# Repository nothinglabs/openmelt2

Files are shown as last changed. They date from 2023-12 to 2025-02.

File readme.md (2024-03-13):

# Open Melt

Open Melt is an open-source translational drift (aka "melty brain") robot controller based on Arduino.

A translational drift robot spins its entire body using its drive wheel(s), but is still capable of directional control by modulating motor power at certain points each rotation.  To achieve this - the rate of rotation must be tracked.

<div align="center">
<table class="center"><tr><td align="center">
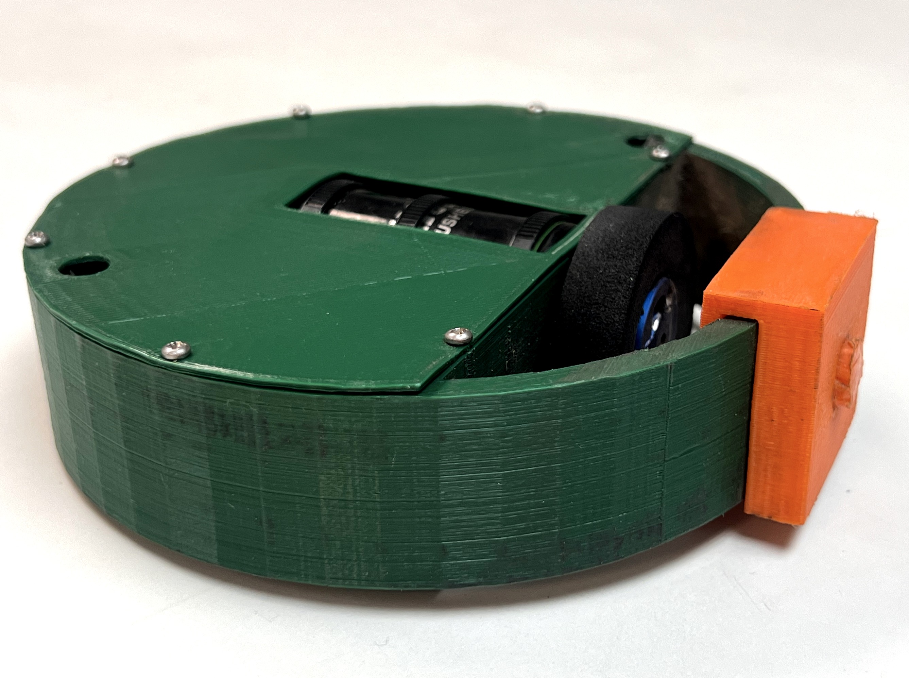
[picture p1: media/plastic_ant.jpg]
<a href="./antweight_reference_platform/"><br>Antweight Reference Platform</a</td>
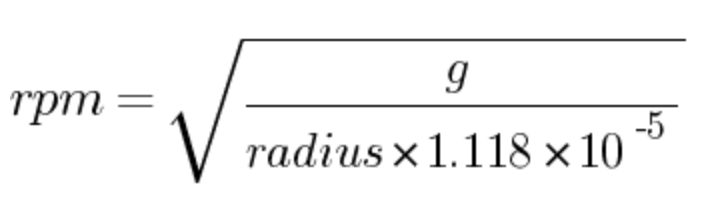
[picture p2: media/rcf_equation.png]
<td valign="center"></td>
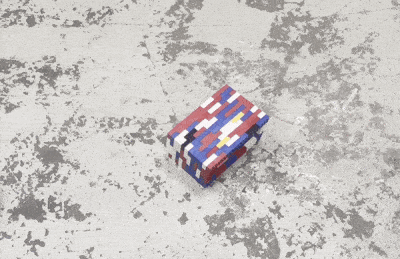
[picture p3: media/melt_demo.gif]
<td align="center"><br>~2300rpm</td>
</td></tr></table></div>

Open Melt uses an accelerometer to calculate the rate of rotation based on G-forces around a given radius (centrifugal force).  For example - an accelerometer mounted 4cm from the center of rotation experiencing 145g can be [calculated](https://druckerdiagnostics.com/g-force-calculator/) to indicate 1800rpm rotation.

An LED is turned on once per rotation - giving the appearance of the "front" of the robot.  This lets the driver see the expected direction of translation.  The user can adjust the heading beacon by moving the remote control left or right.  This allows for steering and correction of minor tracking errors.

The system can work with robots using either one or two drive motors.

It has been tested up to 3200rpm - and can likely work at significantly higher speeds.

Version 2 of the project is a complete recode (previously native Atmega/AVR).  The move to Arduino was done to make it more accessible and potentially portable to non-AVR platforms.

Open Melt was developed by Rich Olson ([nothinglabs.com](http://www.nothinglabs.com) / rich@nothinglabs.com) and is provided under the [Creative Commons Attribution-NonCommercial-ShareAlike](https://creativecommons.org/licenses/by-nc-sa/4.0/deed.en) license.

A longer demo video and some background on Open Melt are available at this [blog post](http://www.nothinglabs.com/open-melt-2/).

#### For a complete parts list, 3d print files and build notes see the [antweight reference platform](./antweight_reference_platform/).

## Demo Video

https://github.com/nothinglabs/openmelt2/assets/3834997/7247756d-c1fe-4b85-9fc3-9274c0709dcb

## General Hardware Requirements

- Arduino Micro (or other Atmega32u4 5v 16MHz Arduino / compatible)
- [H3LIS331](https://www.st.com/resource/en/datasheet/h3lis331dl.pdf) 400g accelerometer (recommended: [Adafruit H3LIS331 breakout](https://www.adafruit.com/product/4627))
- RC Transmitter / Receiver 
- Heading LED
- Motor Driver(s)
- Motor(s)

Use of an **Atmega328-based Arduino is not supported** due to lack of adequate interrupt pins.

The HSLI311 is a 3v part - but the Adafruit breakout includes a 3v<->5v level converter to make interfacing with the Arduino easy.  Alternatively, [Sparkfun's H3LIS331DL Breakout](https://www.sparkfun.com/products/14480) has been verified to work when used in conjunction with the [SparkFun 3v<->5v Logic Level Converter](https://www.sparkfun.com/products/12009).

## 1 vs. 2 Wheels
Open Melt generates signals for 2 motors independent of how many are connected.  Motor 2 is powered for the same portion of each rotation as motor 1 (trailing 180 degrees out of phase).

<div align="center">
<table class="center"><tr><td>
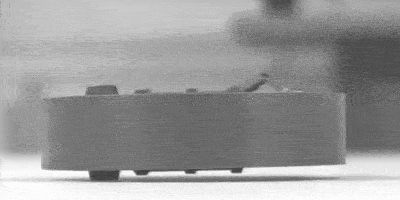
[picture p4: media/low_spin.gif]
</td>

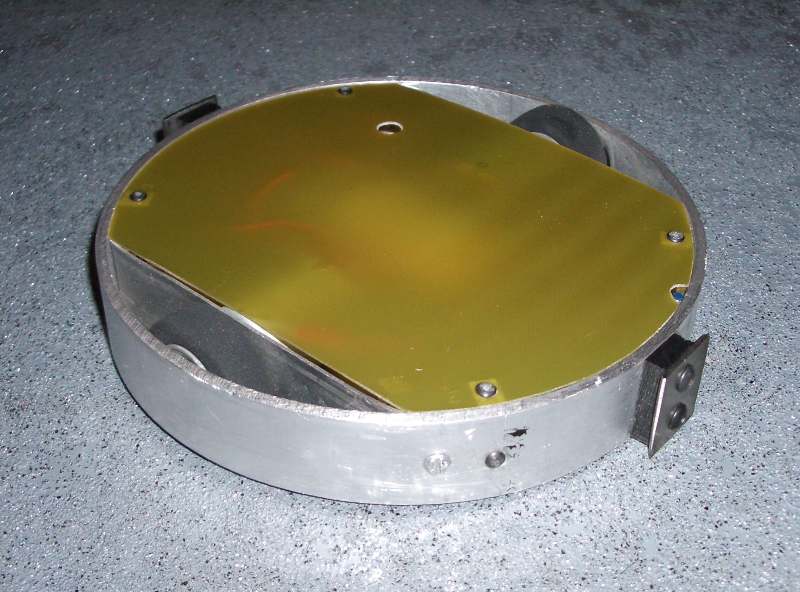
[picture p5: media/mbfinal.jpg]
<td></td>
</td></tr></table></div>

In a 1 wheel robot - the unsupported end scrapes the ground during spin-up - but then levitates when it reaches speed.  

## Accelerometer Placement
The accelerometer must be positioned so that it experiences no more than 400g at the robot's anticipated max rotation speed. A [centrifuge calculator](https://druckerdiagnostics.com/g-force-calculator/) may be used to determine this.

Open Melt provides an interactive setup routine that makes precise placement or orientation of the accelerometer unnecessary.

Alignment of the accelerometer off-axis will result in a linear error - which has the same effect as reducing the radius of rotation.  Placing will the accerometer at a 45 degree angle will effectively halve its sensitivity.  This may be useful in larger robots.

The software also corrects for installing the accelerometer 180 degrees rotated.

## Motor Driver(s) / Throttle Control

Open Melt can generate either a simple on / off motor signal - or provide a 0-100% 490Hz PWM signal.

Either kind of signal may be fed directly to a MOSFET or motor controller that accepts 5v logic-level input.

The antweight reference platform uses a RFP30N06LE N-Channel MOSFET.

Open Melt supports a few different throttle configurations - see [melty_config.h](openmelt/melty_config.h) for details.

In the default BINARY\_THROTTLE mode - the throttle level determines what portion of each rotation the motor(s) are powered (fully) on for.  For example - at 50% throttle the motors would be powered for 180 degrees of each rotation.  At higher throttle settings translation is reduced (with no translation at 100%).

When no forward or back translation is desired - the portion of the rotation that is powered is constantly cycled 180 degrees (cancelling out any translational drift).  

Brushless RC motor controllers that support high-speed 490Hz PWM may work with Open Melt.  A "Hobbypower 30a" brushless controller running the [SimonK firmware](https://github.com/sim-/tgy) has been tested and found to work.  Other controllers running SimonK firmware may also work.

## Heading LED / Visibility

The heading LED should be installed at a location along the perimeter of the robot where it can be viewed at any angle while being driven.  Open Melt's interactive configuration can adjust for any placement.

A common issue is the robot shell or lid obscuring the LED when viewed from shallow angles (such as across an arena).  Raising the LED, or insetting it from the shell perimeter by just a few millimeters can significantly improve visibility.  

The [Arduino Micro is capable of 20ma per I/O pin](https://store.arduino.cc/products/arduino-micro#:~:text=Each%20pin%20can%20provide%20or,permanent%20damage%20to%20the%20microcontroller) - so a resistor must be used to limit LED current.  The 100ohm resistor in the schematic is a good value for blue LEDs.  Values for other color LEDs may be determined using a [LED Series Resistor Calculator](https://www.digikey.com/en/resources/conversion-calculators/conversion-calculator-led-series-resistor).

Selecting an LED with a wide viewing angle will help maximize visibility.

An LED driven at 20ma can be surprisingly bright.  If you need better visibility - a larger LED may be driven using a MOSFET.

## Schematic / Supporting Components

A 10:1 voltage divider is implemented using 2 resistors to allow measuring battery voltage by the Arduino.

The 4700uF capacitor is required across the 5v power bus to assure motor noise does not cause power fluctuations (and unwanted reboots).

If using a MOSFET for motor control - an appropriately sized Schottky diode **must** be installed across the motor leads. 

The receiver and accelerometer are powered via the Arduino's 5v regulator (rated 7-12v input).  Practically - this seems to work well enough with a 7.4v LiPo battery.  For higher voltages - a dedicated voltage regulator should be used (an 11.1v LiPo has a fully-charged voltage of 12.6v).

<p align="center">
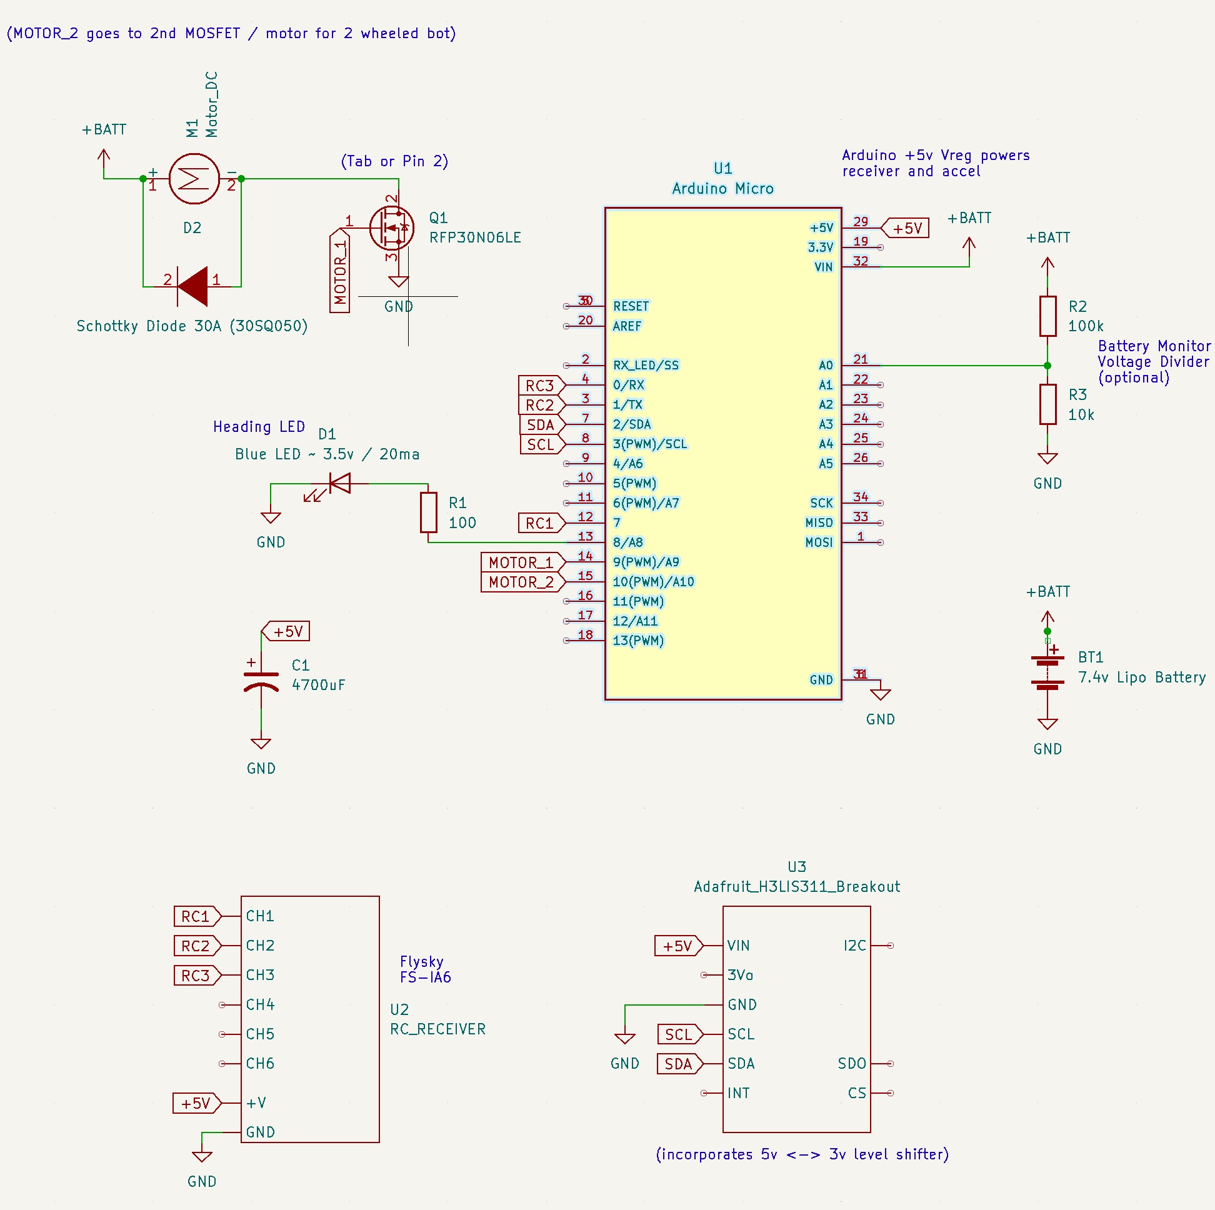
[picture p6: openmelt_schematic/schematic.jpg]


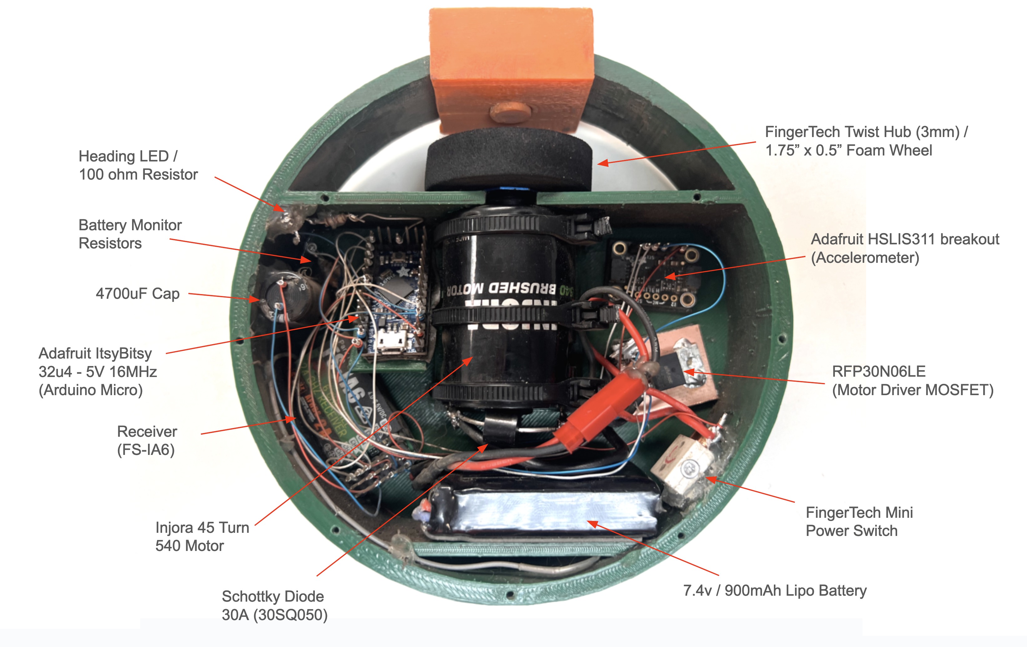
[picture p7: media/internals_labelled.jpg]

</p>

## Remote Control
Open Melt is controlled using a standard hobby RC control system.  3-channels are required (throttle, forward-back and left-right).

Be sure to choose a receiver that supports fail-safe and is configured to set the throttle to 0% (or no signal) in event of radio loss. **Verify it works correctly**. 

The [FlySky i6 transmitter ](https://www.flysky-cn.com/i6-gaishu) and [FlySky iA6 receiver](https://www.flysky-cn.com/ia6-canshu) are inexpensive options that work well (and support fail-safe).

## Safety / Disclaimer

**Building and operating a robot of this type, even in smaller versions, is inherently dangerous. By choosing to use the provided code and plans, you acknowledge the risks involved.  The creator of these plans cannot be held responsible for any injuries, damages, or losses that may result from the use of this project.**

A few mechanisms are implemented with the intent of improving safety.

A [watchdog timer](https://github.com/adafruit/Adafruit_SleepyDog) is used - so if the code unexpectedly becomes trapped - the Arduino should reboot.

At boot-up - it is verified that the RC signal is both good - and that the throttle is at 0% for ~1 second.  This means that if the robot reboots unexpectedly - it can not be spun up again until the driver lowers the throttle for ~1 second.  This behavior may be disabled (see [melty_config.h](openmelt/melty_config.h)).

If no RC updates are received on the throttle channel for ~1 second - the robot should spin down.  It will resume operation when the RC signal is restored **(0% throttle is not required)**.

It should be noted that MOSFET drivers can fail in a "closed" state.  This means that they will drive the motor until the battery runs out.

## Setup Tutorial Video

https://github.com/nothinglabs/openmelt2/assets/3834997/2dc84804-ed5a-4955-8e00-1ae2ac9f0f43

## User Guide

### Stationary Status LED
When sitting idle - the robot will flash one of the following patterns:
<table>
<tr><td>Waiting for Initial RC Signal (0% Throttle Required)</td><td>Slow On / Off</td></tr>
<tr><td>RC Signal Lost</td><td>Slow Flash</td></tr>
<tr><td>RC Good / Ready to Spin-up</td><td>Fast Flash</td></tr>
<tr><td>Configuration Mode</td><td>Double-Flash</td></tr>
</table>

### Configuration Mode

Configuration mode allows interactive setting of correct rotation radius and LED heading offset.  The accelerometer's DC offset (inaccuracy at 0g) is also automatically measured and then compensated for.  Having DEFAULT\_ACCEL\_MOUNT\_RADIUS\_CM set approximately correct in [melty_config.h](openmelt/melty_config.h) can make the setup process easier.

Configuration mode can be entered by pulling the control stick toward the back - and holding it there for ~1 second.

Do not enter configuration mode if the robot is still spinning-down.  Doing so will result in an incorrect accelerometer 0g offset.

To exit configuration mode - pull the throttle to the back for ~1 second again.  Changes to configuration are saved to EEPROM on exit.

### Configuring Tracking Adjustment (radius of rotation)

Once in configuration mode - spin the robot up using the throttle.  Try 30-40% throttle at first.

With the control stick in the neutral forward-back position - move the stick left or right until heading LED tracks a consistent direction.  The heading LED will "shimmer" as it's being adjusted.

Moving the control stick forward will attempt to move the robot forward to test translation.  Moving the stick left / right will steer the robot as it's moving.  

### Configuring Heading Adjustment (LED offset)

If the robot tracks consistently - but forward movement is offset from the LED's position - the LED offset needs to be adjusted.

With the robot spinning - pull the control stick back.  This will cause the robot to translate in the direction it thinks is backwards based on the current heading configuration.

Pull the stick to the left or right lower diagonal corners to adjust heading offset.  The LED will shimmer to indicate that the offset is being changed.

Now - try moving the robot forward again.  Repeat this process until the robot moves forward and back in alignment with the LED beacon.  This will likely take several attempts.

### Driving
Once configured properly - Open Melt drives (mostly) like a regular robot.  Increase throttle to spin-up.  Once spinning - the control stick controls left/right tracking - and forward/back translation.

Throttle settings of over 50% tend to increase rotation speed at expense of translation.

The width of the LED beacon grows and shrinks proportionate to the throttle.  It roughly indicates what portion of each rotation the robot is powered for.

If the robot is not tracking perfectly - minor adjustments may be made using your RC radio left/right trim.  The math is done in a way so that trim adjustments should stay stable even as rotation speed changes.  

### Low Battery Warning
If low voltage is detected - the LED beacon will display a shimmering / pulsing effect.  See [melty_config.h](openmelt/melty_config.h) for battery monitor settings.

This the same shimmering effect used in configuration mode.  To avoid confusion - be sure to have a fully charged battery when using configuration mode.

### Max RPM Report
While spun-down - push the control stick forward for ~1 second.  This will cause the robot to flash out the highest RPM observed in multiples of 100.  For example 23 flashes = 2300rpm.

Entering / exiting config mode will cause this number to be reset to 0.

## 1 Wheel Stability Challenges

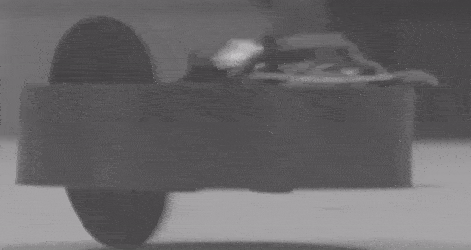
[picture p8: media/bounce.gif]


In some 1 wheel robots - oscillation / bouncing has been observed at higher speeds - which can reduce translational control. This phenomena is not fully understood - but may be caused by too-soft wheels deforming / shifting off the center of the hub. Conversely - harder wheels may cause this problem when they bounce off imperfections in the floor.

2 wheel designs seem less prone to these issues (but are slightly less cool looking).

Robots with lower ground clearance seem to experience this problem less.  The antweight reference platform is fairly stable up to about 2800rpm.

Some examples / more speculation on causes in this video:

https://github.com/nothinglabs/openmelt2/assets/3834997/6260f55a-6395-46f6-a2f1-cd301056c252

## Motor Timing Video
This video attempts to demonstrate motor power timing relative to the direction of translation.  It is not entirely intuitive.

https://github.com/nothinglabs/openmelt2/assets/3834997/cda94d4d-d73b-48d2-b551-4b090d01f84a

## Arduino Notes
This project uses both the "RX" and "TX" (pins 0 and 1) on the Arduino.  With Atmega32u4 Arduinos this does not interfere with programming.

Open Melt uses the [Adafruit SleepyDog](https://github.com/adafruit/Adafruit_SleepyDog) to implement the watchdog timer.

The [SparkFun\_LIS331](https://github.com/sparkfun/SparkFun_LIS331_Arduino_Library) library is used to interface with the H3LIS331 accelerometer.  This library seems to not deal with all I2C failures gracefully - and appeared to be the causes of a hang / run-away in one prototype which was determined to have an I2C wiring issue.  Modifying the library to implement [setWireTimeout](https://www.arduino.cc/reference/en/language/functions/communication/wire/setwiretimeout/) might address this specific issue.  The watchdog timer was implemented to deal with this and any similar issues.

Versions of both libraries last verified to work with Open Melt are archived in the arduino\_library\_archives folder.

A significant power glitch could cause the Arduino Micro to go into a 7-second delay on reboot waiting to be programmed.  In a combat robot event - this could certainly result in a lost fight.  It should be possible to address this issue by [bypassing the bootloader and burning the sketch directly](https://docs.arduino.cc/hacking/software/Programmer) (this has not been tested).

Open Melt has not been tested on non-AVR Arduinos - but may work with some minor limitations.  See [melty_config.h](openmelt/melty_config.h) for details.

## Troubleshooting
When throttle is at 0% - Open Melt will log out diagnostics data (RC data, accelerometer status, configuration parameters, etc.) via serial USB.  This may be viewed by using Arduino's "Serial Monitor" (115kbps).

Note: Connecting the Arduino to USB may put it in an unexpected state - **which could cause the motor(s) to spin up**.  Only connect your Arduino to USB if the battery powering the motor is disconnected.

***

#### For Open Melt version 1 (obsolete!) - [see here](http://www.nothinglabs.com/openmelt_legacy/).

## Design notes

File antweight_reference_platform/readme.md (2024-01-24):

# Open Melt Antweight Reference Platform

This robot was created as an easy-to-build, 3d-printed test platform for Open Melt.  All design files are provided.

Being Arduino based - no special programmer is required.  No custom PCB's or fine-pitch soldering is needed.  All components are readily available as of this writing.

It is intended to comply with [Plastic Antweight combat robot rules](https://www.westernalliedrobotics.com/index.php/the-rules/special-plastic-class-rules).  The total weight of the test build is about 0.5oz under the 16oz weight limit.

This robot can spin up to around 3000rpm.  It is capable of causing projectiles that could seriously injure someone.  It is recommended you only test inside an enclosed arena.

The option for a removable weapon is intended to provide a less-scary way to test a melty brain robot.  Proper precautions should still be taken.

This robot has not yet been battle tested.

<div align="center">

</div>

## Parts List
- [Arduino Micro](https://store.arduino.cc/products/arduino-micro) or [Adafruit ItsyBitsy 32u4 - 5V 16MHz](https://www.adafruit.com/product/3677)
- [Adafruit H3LIS331 breakout](https://www.adafruit.com/product/4627)
- RFP30N06LE N-channel MOSFET (widely available)
- [30SQ045 Schottky Diode](https://www.digikey.com/en/products/detail/anbon-semiconductor-int-l-limited/30SQ045/18800935)
- 3mm blue LED (rated 20ma or higher)
- [FlySky i6 transmitter ](https://www.flysky-cn.com/i6-gaishu) and [FlySky iA6 receiver](https://www.flysky-cn.com/ia6-canshu)
- 45-turn 540 size RC car motor
- [FingerTech Mini Power Switch](https://www.fingertechrobotics.com/proddetail.php?prod=ft-mini-switch)
- [FingerTech Twist Hub (3mm / 0.5")](https://www.fingertechrobotics.com/proddetail.php?prod=ft-twist-hubs)
- [FingerTech Foam Wheel (1.75" x 0.5")](https://www.fingertechrobotics.com/proddetail.php?prod=ft-foam-wheels)
- ~900ma 7.4v lithium polymer battery
- 4700uf electrolytic capacitor (30mm or shorter for easy fit)
- 100, 10k and 100k Ohm resistors

## Fasteners / Tools / Misc.:
 - [\#2-28 x 1/4" Phillips Screws](https://www.mcmaster.com/products/plastite-screws/screw-size~no-2/length~1-4-2/length~0-25/)
 - Zip ties
 - Mounting tape (Scotch Extreme or similar)
 - Hot glue gun ("hot" melt as opposed to "low" melt)
 - Small piece of PCB blank or copper sheet
 - Access to a 3d-printer / PLA filament
 - [Wire wrapping tool](https://www.amazon.com/Wire-Wrap-Gauge-ELECTRONIX-EXPRESS/dp/B00BFYE0CY/)

## Overview / Weight Budget

<div align="center">

</div>

| Component | Weight (grams) |
|---|---|
| Shell | 140 |
| Lid | 18 |
| Motor | 172 |
| Battery | 46 |
| MCU | 3 |
| RC Receiver | 2 |
| Mosfet + heatsink | 6 |
| Wires, LED, diode, switch | 4 |
| Wheel + hub | 9 |
| Weapon + pin | 30 |
| Power switch | 4 |
| 4700uf capacitor | 4 |
| **Estimated Total** | **438** |
| **Measured Total (fully assembled)** | **440 (15.5oz)** |

## 3d Model / OpenSCAD
The body of this robot was designed in [OpenSCAD](https://openscad.org/) (programmatic CAD).  You can easily change parameters to adjust things like shell thickness and diameter.

<table><tr><td>
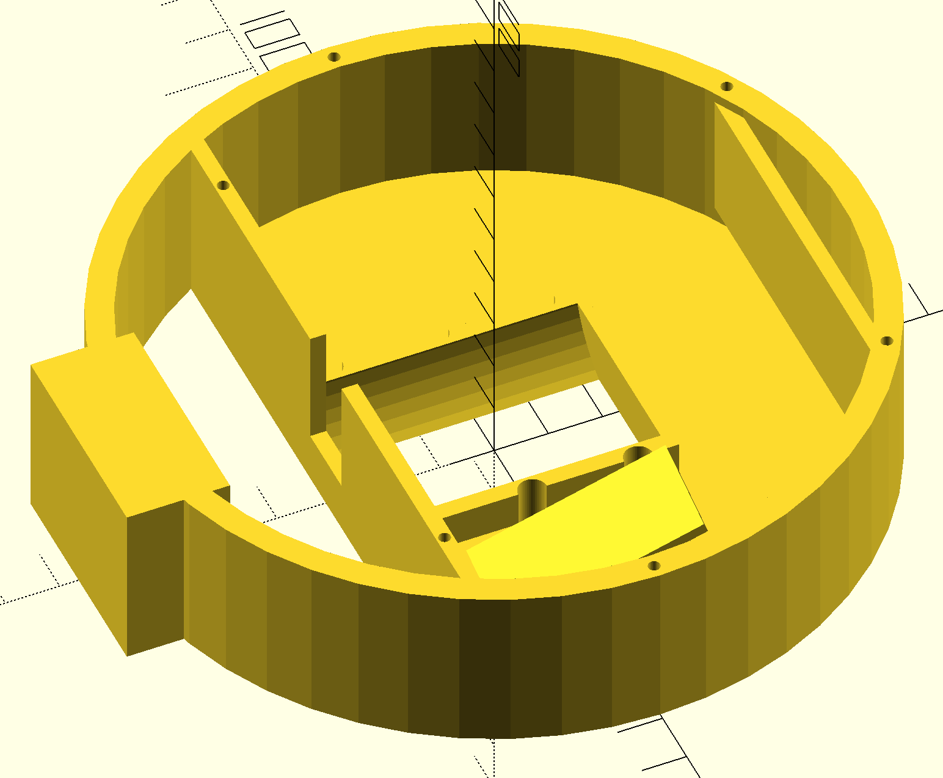
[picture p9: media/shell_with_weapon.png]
</td><td>

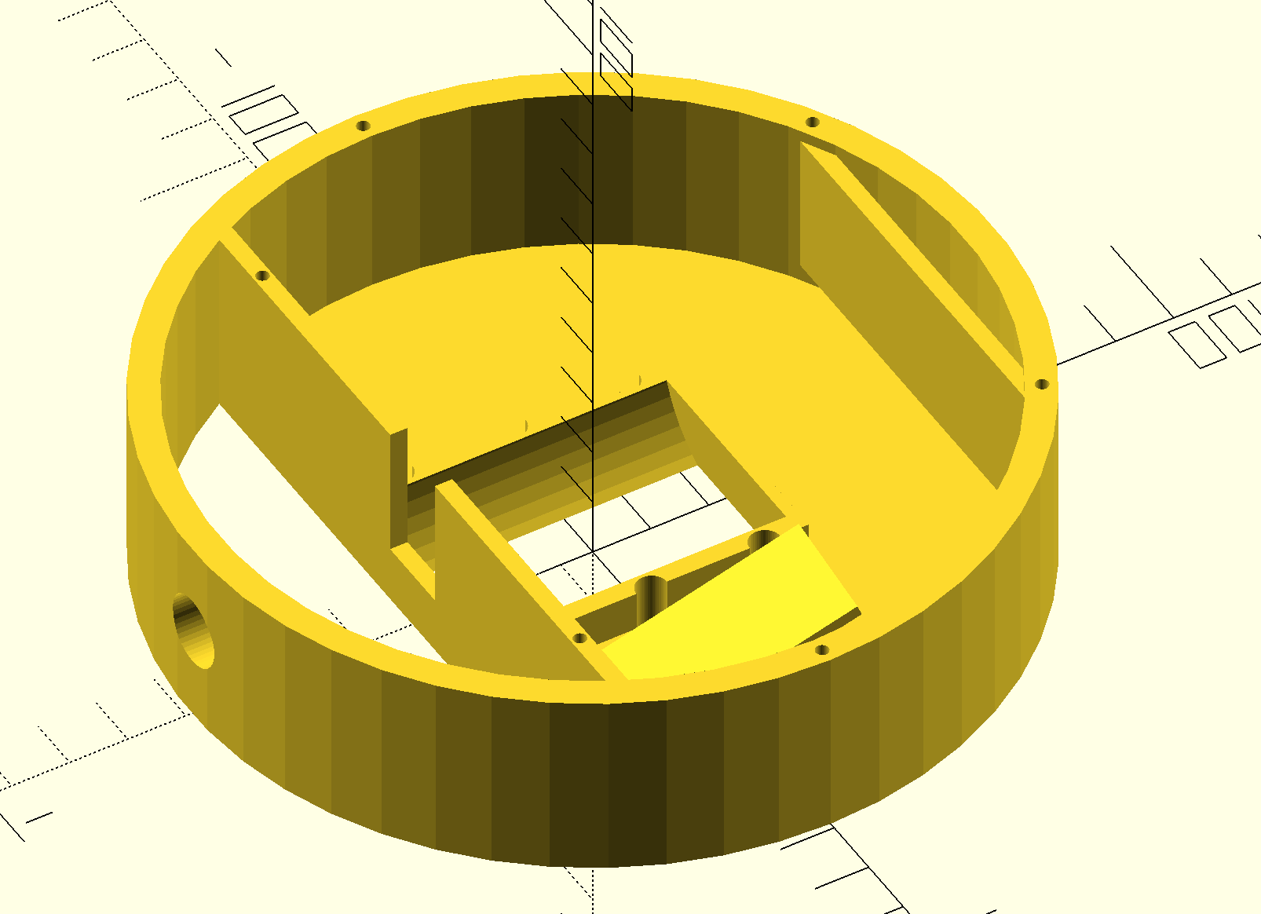
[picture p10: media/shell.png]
</td>
</tr><td colspan="2" align="center">
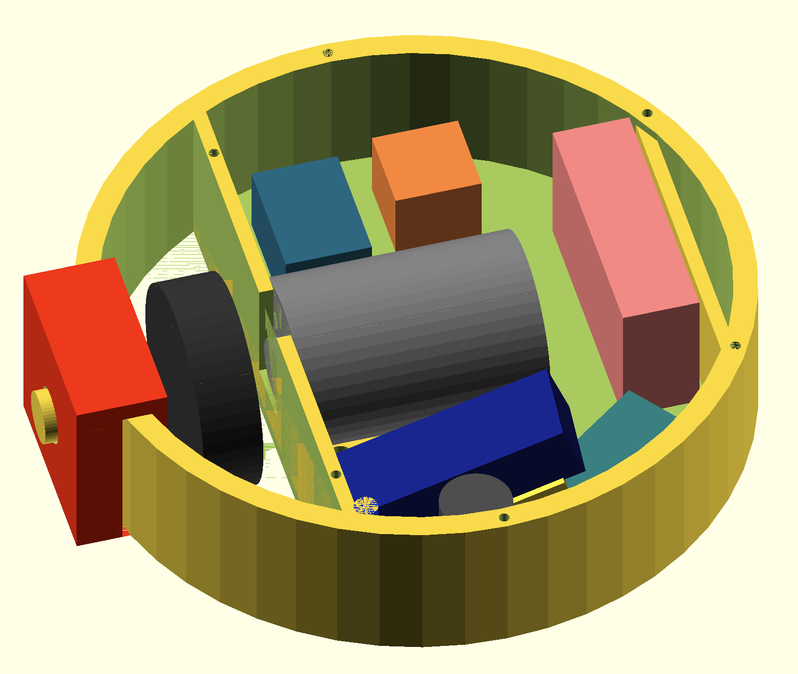
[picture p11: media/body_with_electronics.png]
</td></tr>
</table>

Stand-ins for electronics can be rendered to verify everything fits as intended.

The following STL files are provided for 3d-printing:

| Component | File |
|---|---|
| Robot shell without weapon (weapon mounting hole) | shell\_no\_weapon.stl |
| Detachable weapon | weapon.stl |
| Weapon mounting pin | weapon\_pin.stl |
| Robot lid | lid.stl |
| Robot shell with integrated weapon | shell\_with\_weapon.stl |

## 3d Printing Notes
The test build of the robot is printed in PLA with 100% infill.

For best strength, use a high shell count (5+) and avoid using a cooling fan.

## General Construction
The lid is held on with \#2 screws.  They seem to self-tap pretty effectively.

The accelerometer, motor driver, Arduino and battery are all secured using double-sided tape.

The Arduino is installed on a special shelf that rises up from the floor at an angle.  This allows a USB cable to be attached to it for programming after assembly.

The battery is taped both against the floor of the robot - and the flat section of wall behind it.  There is clearance under the flat wall for a zip-tie if more security is desired (good idea).

The power switch, LED, capacitor and resistors are all held in place with hot glue.

The motor is held into place using zip ties.

This all seems to work - at least for testing purposes.  You might have better / more robust ideas.

<table><tr><td>
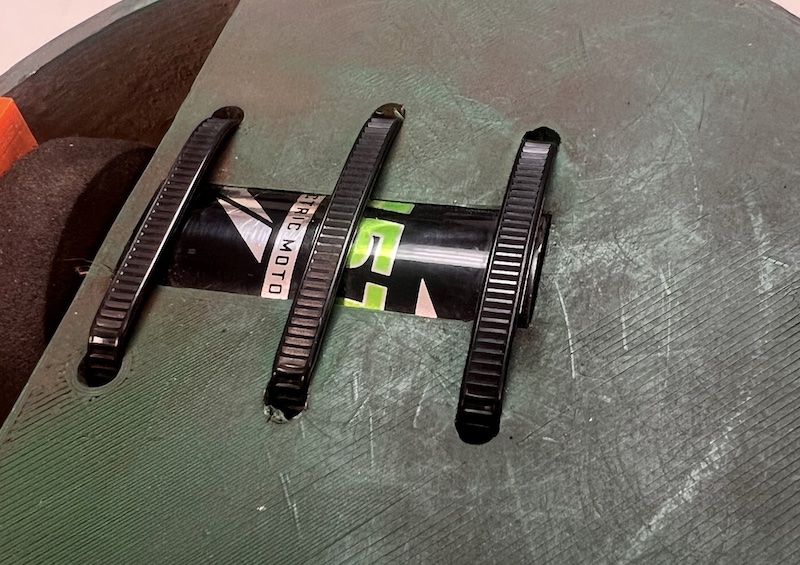
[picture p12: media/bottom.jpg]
</td><td>

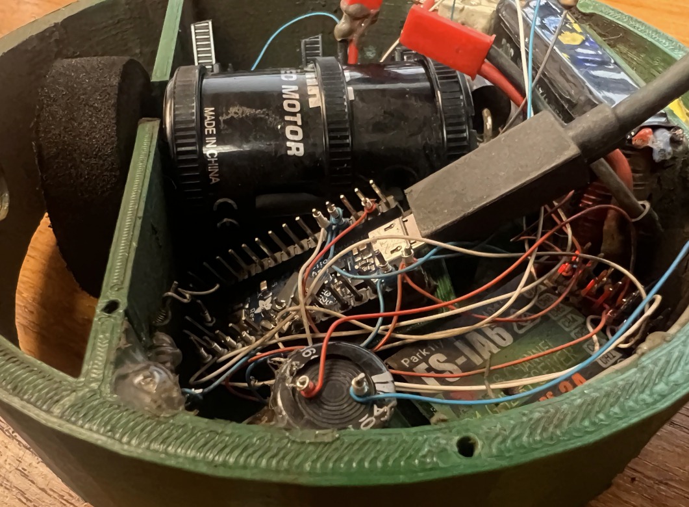
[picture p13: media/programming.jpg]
</td>
</tr>
</table>

## Detachable Weapon

A shell option without a built-in weapon is provided.  Building the robot without a weapon is a good way to test with reduced "drama."

This shell includes a mounting hole so that a weapon may be attached later using a press-fit pin.  No assurances are given about the robustness of this approach.  Using hot-glue to re-enforce weapon attachment may prove useful.

<table><tr><td>
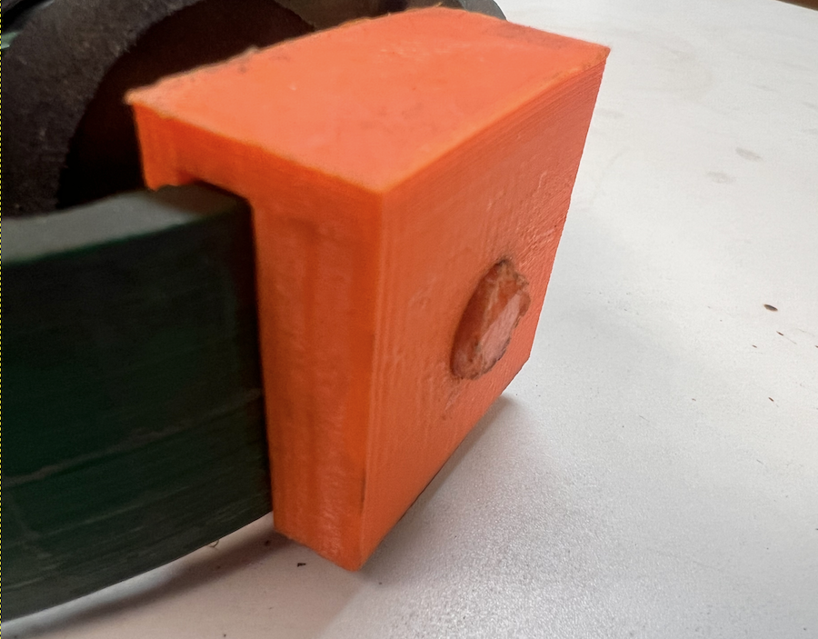
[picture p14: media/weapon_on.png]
</td><td>

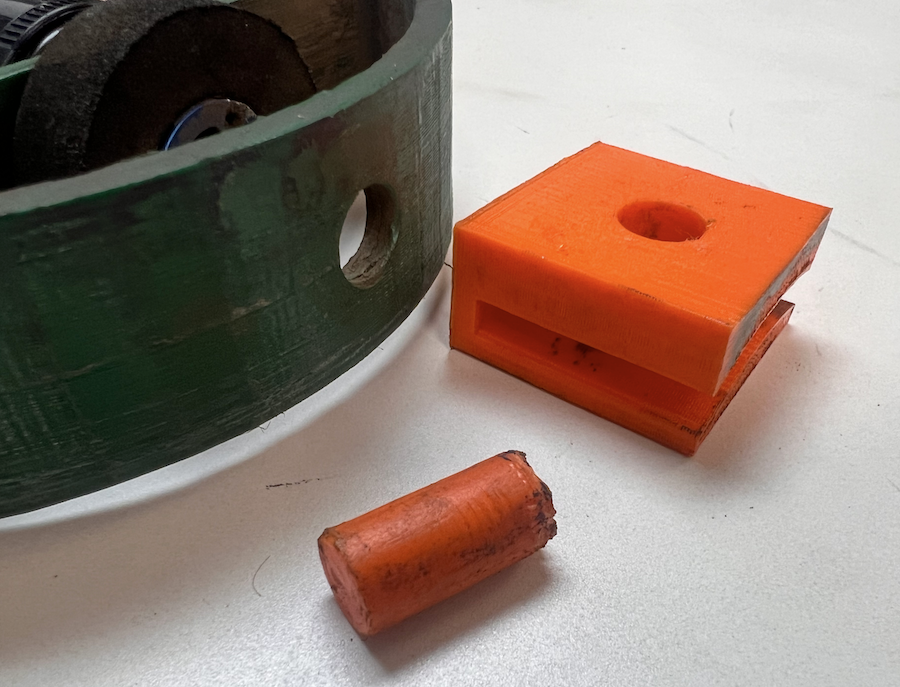
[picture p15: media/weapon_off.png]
</td>
</tr>
</table>

## Motor 
A 45-turn 540-sized "sealed endbell" hobby motor is used.  [Injora](https://www.amazon.com/INJORA-Brushed-Tracks-AXI03007-Parts%EF%BC%8845T%EF%BC%89/dp/B08X21JCGZ/?th=1) is one of many common brands.

The number of turns determines how fast the motor rotates for a given voltage.  Lower turn motors spin faster and draw more current.  A 45-turn motor is considered a slower "torque / crawler" motor.  

Using a lower turn motor has not been tested - and may overtax the MOSFET.

The 30SQ045 Schottky diode must be soldered across the motor leads as indicated in the schematic - or the MOSFET will quickly be destroyed by back-voltage.

## Wheel Hub
The wheel hub is specified as 3mm, where the motor has a shaft of 3.175mm (1/8").  It will need to be very slightly drilled out.
<div align="center">

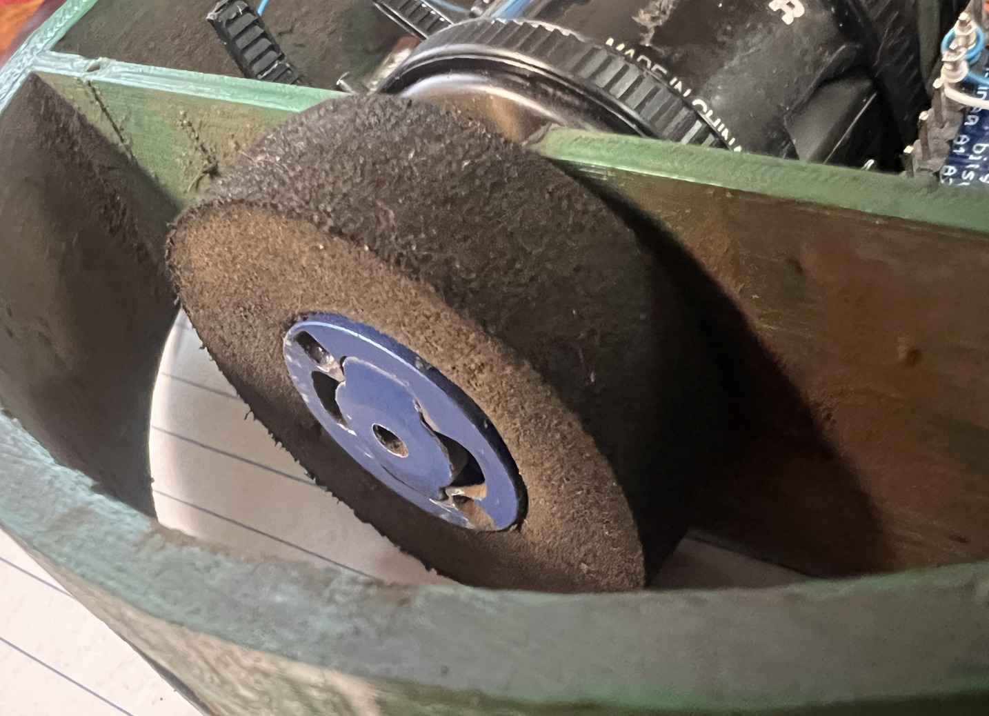
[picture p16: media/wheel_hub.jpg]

</div>

## Battery
The [7.4v 900mAh battery](https://www.amazon.com/dp/B09BYVNH2N?psc=1&ref=ppx_yo2ov_dt_b_product_details) used for the test build is specified as 53x29x16mm (46 grams).  The key dimension is that it needs to be < 30mm wide in order to fit as oriented.

Runtime on a full battery charge is over 6 minutes.  A somewhat smaller battery could probably be used.

Upgrading to a 11.1v battery may be possible - but some preliminary tests suggested it may be too much for the MOSFET to handle.  A dedicated voltage regulator is recommended for voltages over 7.4v.

## Schematic

Wire it up like this...
<div align="center">


</div>

## Wiring Things (Wire Wrap)
Using ["wire wrap"](https://learn.sparkfun.com/tutorials/working-with-wire/how-to-use-a-wire-wrap-tool) for all signal and low-power connections is recommended.  When done properly wire-wrap connections are reliable and provide strain relief.  The small gauge wires minimize the stress put on connections under the stresses experienced by a melty bot.

<div align="center">
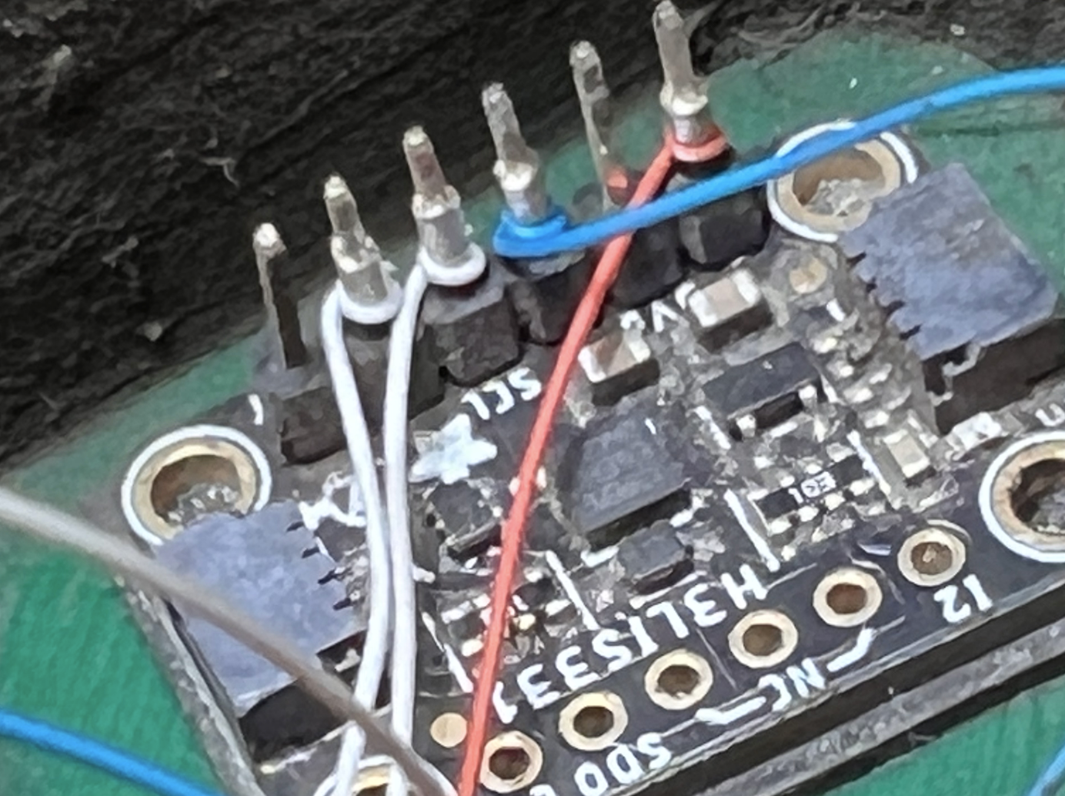
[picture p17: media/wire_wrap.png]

</div>

Wire wrapping has fallen out-of-fashion - but there is a reason they used this approach for the [Apollo Guidance Computer](http://www.righto.com/2019/07/software-woven-into-wire-core-rope-and.html).

If using another wiring method - just keep in mind the high forces this robot will experience.  Temporary "Dupont wire" jumpers are not likely to work reliably.

## Heading LED / Visibility
The heading LED and resistor are hot glued into the upper-left corner of the robot.  

Glue the LED close to the top of the shell (away from the floor).

The lid / shell edge can potentially obscure LED visibility.  Mounting the LED so it slightly protrudes above the shell edge (flush with the lid) can help with this.

Be sure to test with the lid on to verify good LED visbility.

Make sure to glue the resistor to a surface so that it doesn't place strain on the LED or wiring.

<div align="center">
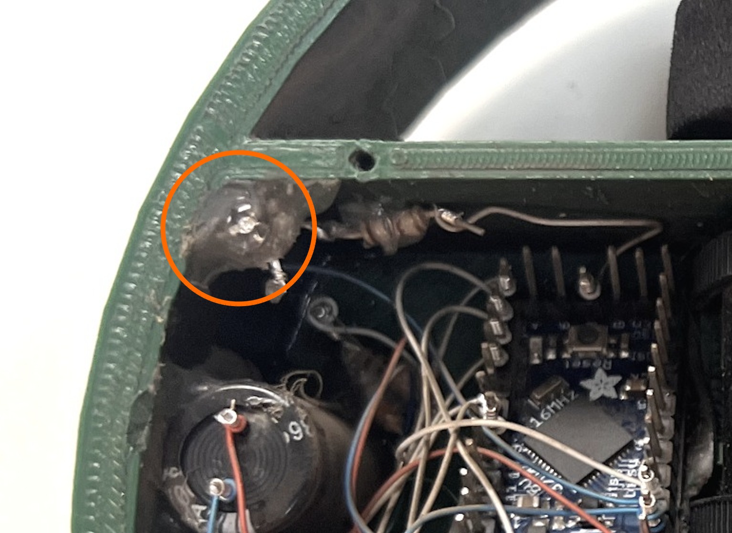
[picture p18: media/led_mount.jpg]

</div>

## Motor Driver

The RFP30N06LE is a widely available N-channel MOSFET.  The original FairChild / onsemi version seems discontinued - but many manufacturers still make versions of it.

Cut a small piece of PCB blank or thin copper sheet - and solder the tab of the RFP30N06LE to it.  This will provide a crude heatsink.

The tab is electrically equivalent to the middle pin.  The motor may be directly connected to the copper PCB surface (the middle pin may be cut off).

The PCB blank / copper sheet provides adequate surface area to be mounted using double-sided tape.

<div align="center">
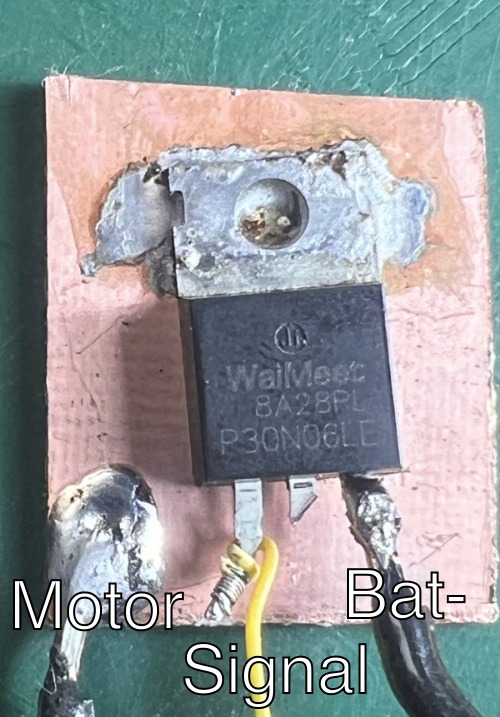
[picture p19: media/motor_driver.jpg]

</div>

## Battery Voltage Monitor
Two resistors (10k and 100k Ohm) as shown in the schematic are required to create the 10:1 voltage divider needed for battery monitoring / alarm.

These can be hot-glued someplace convenient in the chassis.

The voltage monitor is optional - but a good idea to avoid over-discharging your battery.

See BATTERY\_ALERT\_ENABLED and BATTERY\_ADC\_WARN\_VOLTAGE\_THRESHOLD in [melty_config.h](../openmelt/melty_config.h) for options.

## Deploying Firmware

Get the latest version of the [Arduino IDE](https://www.arduino.cc/en/software).

You will need to also download and install the [Adafruit SleepyDog](https://github.com/adafruit/Adafruit_SleepyDog) and [SparkFun_LIS331](https://github.com/sparkfun/SparkFun_LIS331_Arduino_Library) libraries.

Select board type as "Arduino Micro" - and you should be ready to deploy the firmware.

The constants in [melty_config.h](../openmelt/melty_config.h) are intended to reflect the test platform - so the interactive configuration process should be fairly smooth.



## Optional Motor Modification

A 1-wheel robot results in a constant pulling force on the motor as it rotates.  This will cause the motor shaft to become loose over time (specifically - there is an internal shim on the shaft that slips).  These motors tend to still run - but are noisy, slower and less efficient.

One solution is to just replace the motor when it gets worn-out.  At about $15 - this is a pretty good option.

<div align="center">
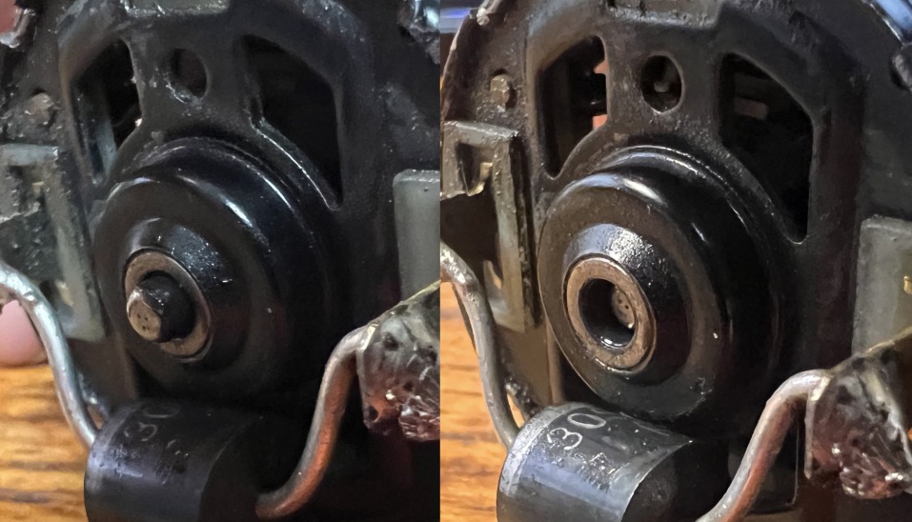
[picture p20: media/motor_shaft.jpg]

<p>Worn motor showing ~2mm play in shaft</p></div>

A modification that seems to help with this problem is placing a 3.2mm inner-diameter plastic washer on the rear-end of the shaft - and then soldering a metal 3.2mm inner-diameter washer on top of it to sandwich it in place.

<div align="center">
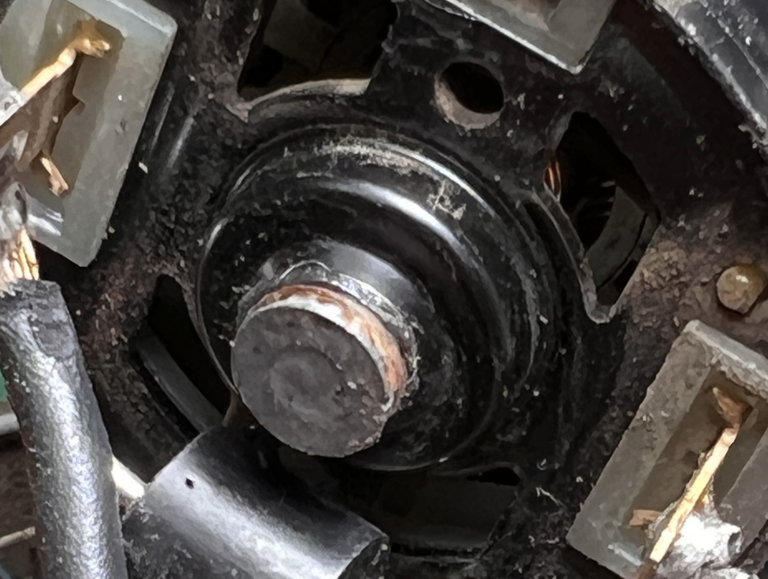
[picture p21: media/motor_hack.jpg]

<p>Motor with soldered retaining washer / plastic glide washer</p>
</div>

A high temperature soldering gun and use of flux will help assure a good solder bond is quickly made - and reduce the chance of completely melting the plastic washer.

For the test build these parts were sourced from an already damaged 540 motor.

These parts from McMaster Carr have not been tested - but may provide similar functionality:  
[https://www.mcmaster.com/95395A104/](https://www.mcmaster.com/95395A104/)  
[https://www.mcmaster.com/93785A821/](https://www.mcmaster.com/93785A821/)

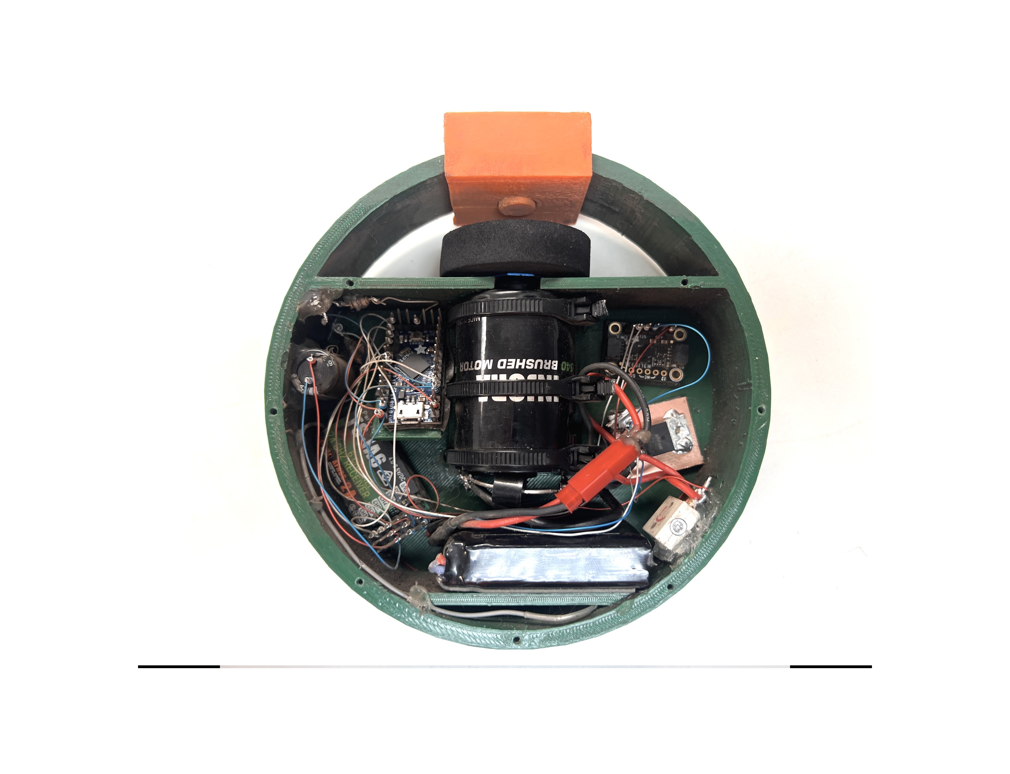
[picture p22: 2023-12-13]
media/plastic_ant_internals.jpg

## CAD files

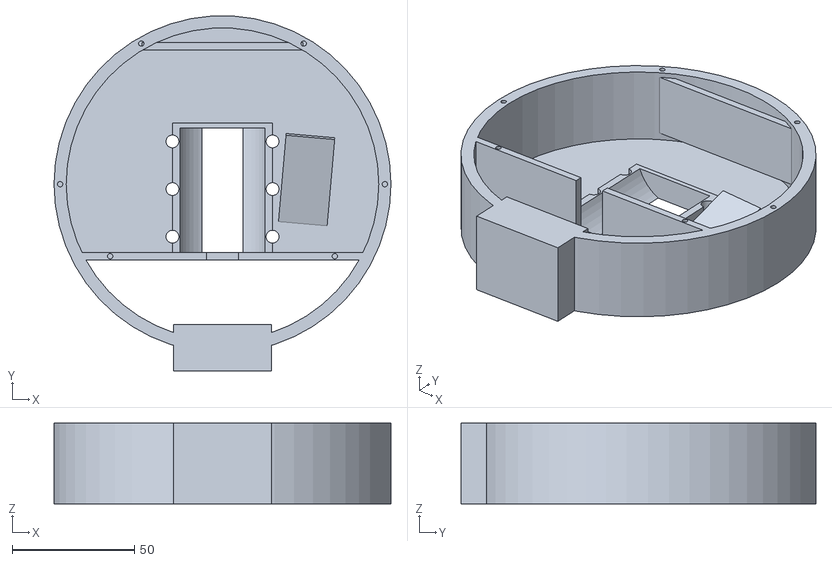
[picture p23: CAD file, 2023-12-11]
antweight_reference_platform/shell_with_weapon.stl
138.0 x 145.4 x 33.0

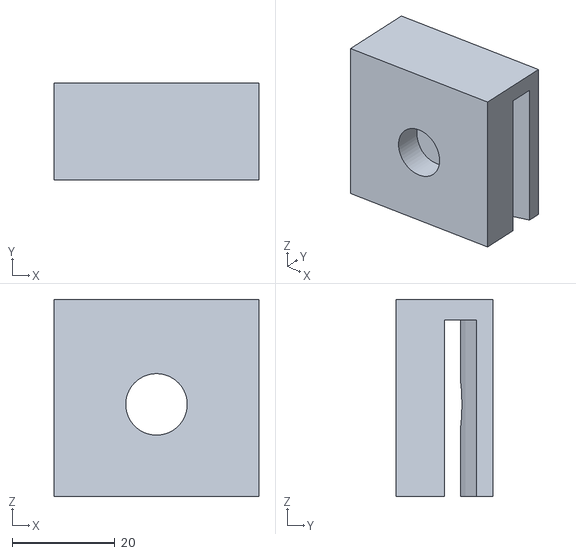
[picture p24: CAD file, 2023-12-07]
antweight_reference_platform/weapon.stl
40.0 x 19.0 x 38.5

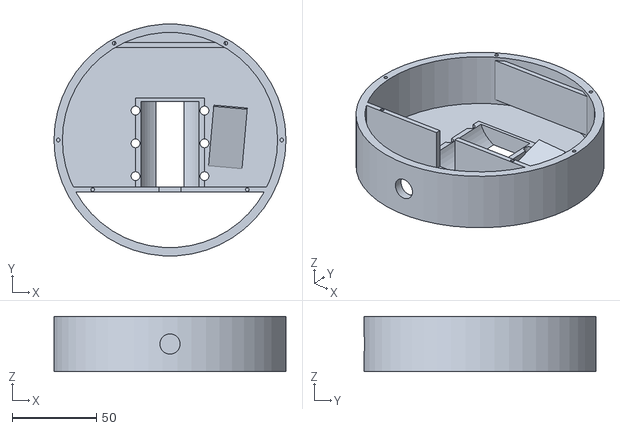
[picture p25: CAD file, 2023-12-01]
antweight_reference_platform/shell_no_weapon.stl
138.0 x 137.7 x 33.0

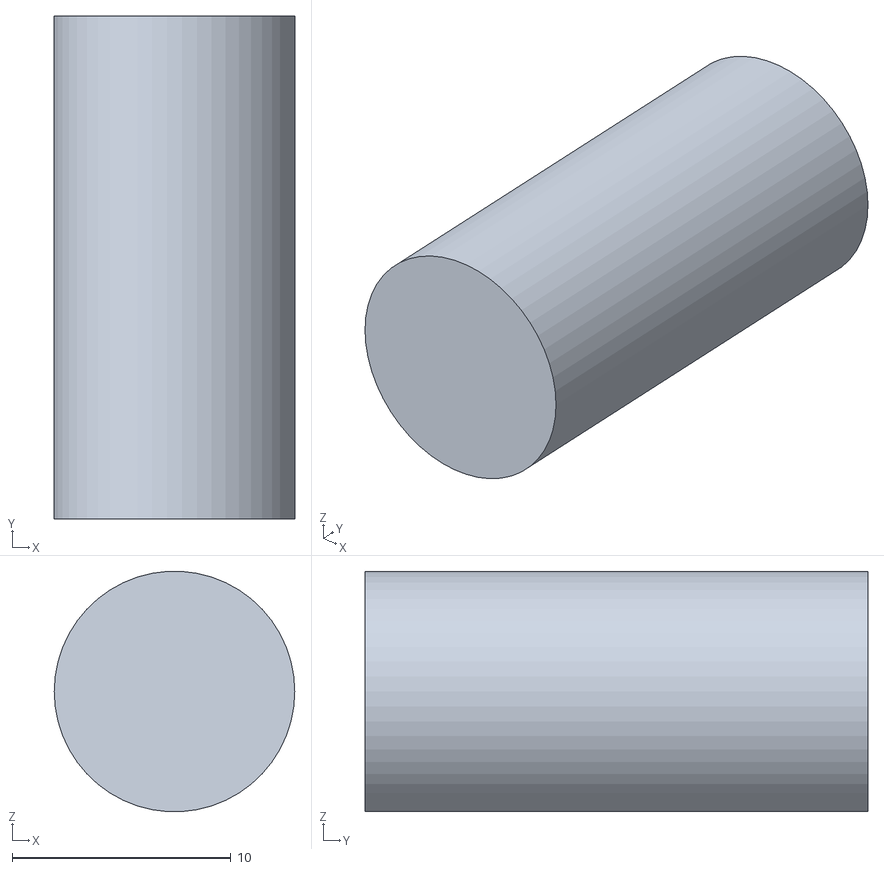
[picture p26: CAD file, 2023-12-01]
antweight_reference_platform/weapon_pin.stl
11.0 x 23.0 x 11.0

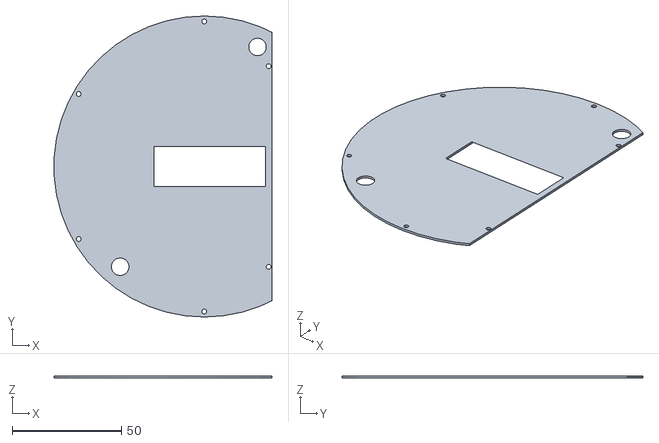
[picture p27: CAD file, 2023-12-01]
antweight_reference_platform/lid.stl
99.9 x 138.0 x 1.00

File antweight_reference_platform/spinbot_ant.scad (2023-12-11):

weaponPartOfBody = false;   //render the weapon and the body together

renderBotBody = true;     //render the main shell or not
renderLid = false;           //render the lid of not
positionLidForPrint = true;  //if false - lid renders on top of the bot

renderWeapon = true;
renderWeaponPin = true;        

includeWeaponMountHole = weaponPartOfBody ? false : true;

renderArduinoShelf = true;  //HARDCODED shelf for Arduino to make USB port accessable while installed in bot
includeBatteryWall = true;     //parameters for this are HARDCODED
makeTapHoles = true;

//battery wall, weapon, electronics all have hard coded coordinates / sizes (need to tweak functions manually)
renderElectronics = true;
renderMotor = true;
renderWheel = true;

botHeight = 33;
botDiameter = 138;
botShellThickness = 5; 
floorThickness = 3; 
lidThickness = 1; 

motorDepthBelowFloorSurface = 5;    //motor mounts this deep below floor

wheelDiameter = 44;   
wheelWidth = 12.5;
wheelDistanceFromMotorWall = 8;

motorWallThickness = 3; 
motorWallOffset = 28;   //offset of motor wall relative to center of bot

motorDiameter = 37;  //bumped up by 1mm to assure easy mount
motorBushingDiameter = 13; 
motorBushingHeight = 2; 
motorLength = 51; //bumped up by 1mm to assure easy mount

motorMountHeight = 7;
motorMountLength = motorLength + 4; 
motorMountWidth = motorDiameter + 4; 
motorMountOffset = -2;

weaponMountHoleDiameter = 12;
weaponPinExtraLength = 5;
weaponPinDiameterReduce = 1;  //reduces diameter of weapon pin to account for 3d printing kerf

weaponTopVerticalExtension = weaponPartOfBody ? 0 : 4;  //weapon extends this much above shell
weaponBottomVerticalExtension = weaponPartOfBody ? 0 : 1.5;  //weapon extends this much below shell
weaponSlotExtraWidth = weaponPartOfBody ? 0 : 1.0;  //increases width of weapon slot (mm) to account for 3d printing kerf
weaponThickNess = 19;
weaponWidth = 40;
weaponInset = 2;


lidMotorCutWidthAdjustment = 1.5; //adjusts height of motor cut in lid to allow easy clearance (as if motor has been moved upwards by this many mm)

motorMountHoleOffset = 6;
motorMountHoleDiameter = 5.25;

lidScrewHoleDiameter = 2.2;        //diameter for self-tapping screws in print
lidScrewHoleDepth = 10; 

ledAndPowerHoleDiameter = 4;

motorWallWidth = (2 * ((botDiameter / 2)^2 - (motorWallOffset+motorWallThickness)^2)^0.5) - (botShellThickness);

powerHoleOffsetAngle = 140;
ledHoleOffsetAngle = -24;


$fn = 50;

if (renderLid) lid();

if (renderWeapon) {
    if (!weaponPartOfBody) color([1.0,0.0,0.0]) weapon();
    else weapon();
}

if (renderWeaponPin && !weaponPartOfBody) weaponPin();

if (renderBotBody) {

    motorWall();

    if (renderArduinoShelf) arduinoShelf();
    if (renderElectronics) dummyElectronics();

    //HARDCODED battery wall
    if (includeBatteryWall) {
        translate([-33,58,floorThickness + 3]) rotate ([90,0,0]) cube([66,botHeight - 8,3]);
    }

    if (renderMotor) {
        translate ([0, motorMountOffset + ((motorMountLength - motorLength) / 2),floorThickness])
           color([0.5,0.5,0.5]) motor();
    }

    if (renderWheel) {
        translate ([0,motorMountOffset,floorThickness - motorDepthBelowFloorSurface])
            color([0.2,0.2,0.2]) wheel();
    }
    

    //motor mount
    difference() {
        translate ([0,motorMountOffset,floorThickness]) motorMount();
        makeZipTieHoles();
    }

    //actual main body
    difference() {                

        mainShell(botHeight);
        makeZipTieHoles();

        translate ([0, motorMountOffset + ((motorMountLength - motorLength) / 2),floorThickness])
            motor();

        if (makeTapHoles) makeTapHoles();   
        
        if (includeWeaponMountHole) weaponMountHole();
    }

}

module mainShell(height) {
    difference() {
        cylinder(height,botDiameter / 2,botDiameter / 2);
        translate ([0,0,floorThickness]) cylinder(height, (botDiameter / 2) - botShellThickness,(botDiameter / 2) - botShellThickness);
        wheelWellCut();
    }

}


module motorWall() {
    difference() {
        translate([motorWallWidth / - 2,motorWallOffset * -1,0]) rotate ([90,0,0])
            cube([motorWallWidth,botHeight, motorWallThickness]);

            translate([motorBushingDiameter / -2,motorWallOffset * -1, motorMountHeight + floorThickness])
                rotate ([90,0,0])
                    cube([motorBushingDiameter, botHeight, motorWallThickness * 1]);
        if (makeTapHoles) makeTapHoles();

    }
}

module wheelWellCut() {
    intersection() {
        //remove wall thickness for top piece
        translate ([0,0,0]) cylinder(botHeight, (botDiameter / 2) - botShellThickness, (botDiameter / 2) - botShellThickness);
        translate([botDiameter / -2,(motorWallOffset * -1) - motorWallThickness,0])
            rotate ([90,0,0]) cube([botDiameter,botHeight,botDiameter]);
    }
}

module arduinoShelf()
{
    translate([46,19,15]) rotate ([-21,0,175])  cube([20,38,2]);
    translate([46,19,0]) rotate ([0,0,175]) translate([0,13,0]) cube([20,2,10]);
}


module dummyElectronics() {
    //LED
    color([0.1,0.1,0.8]) translate([56,-26,botHeight -5]) rotate ([0,0,0])  cylinder(d = 5, h= 5);

    //capacitor
    color([0.3,0.3,0.3]) translate([56,-3,floorThickness]) rotate ([0,0,0])  cylinder(d = 15, h= 25);

    //battery
    color([1.0,0.5,0.5]) translate([-34,54,floorThickness]) rotate ([90,0,0])  cube([53,29,16]);

    //motor driver (Mosfet + PCB heatsink)
    color([1.0,0.5,0.2]) translate([-55,24,floorThickness]) rotate ([90,0,0])  cube([18,15,18]);

    //rx placeholder (Flysky FS-iA6 Receiver)
    color([0.1,0.5,0.5]) translate([60,20,floorThickness]) rotate ([0,0,127])  cube([40,21.1,7.5]);

    //Adafruit ItsyBitsy 32u4
//    translate([45,18,15]) rotate ([-21,0,175])  cube([18,35,13]);
    
        //arduino micro 
    color([0.1,0.1,0.5])translate([45,23,18]) rotate ([-21,0,175])  cube([18,48,13]);


    //accelerometer (Adafruit H3LIS331)
    color([0.1,0.4,0.5]) translate([-52,-20,floorThickness]) rotate ([0,0,0])  cube([26,18,15]);
    
}


module lid() {
    translate([0,positionLidForPrint ? botDiameter + 1 : 0,positionLidForPrint ? 0: botHeight]) rotate([0, 0, positionLidForPrint ? 90 : 0]){
        difference() {        
            cylinder(lidThickness,botDiameter / 2,botDiameter / 2);
            if (makeTapHoles) {
                translate([0,0,(botHeight * -1) + lidThickness])
                makeTapHoles();   
            }
            
            translate([0,0,(botHeight * -1) + lidThickness])
            makeLedAndPowerHoles();

            wheelWellCut();
            
                translate ([0, motorMountOffset + ((motorMountLength - motorLength) / 2),floorThickness + (botHeight * -1) + lidMotorCutWidthAdjustment])
        motor();
                
            translate([botDiameter / -2,(motorWallOffset * -1) - motorWallThickness,0])
                rotate ([90,0,0]) cube([botDiameter,botHeight,botDiameter]);

        }
    }
}

module makeZipTieHoles(){
        holeOutset = (motorDiameter / 2) + 2;
                
        translate([holeOutset,motorMountOffset + ((motorLength /  2) - motorMountHoleOffset),0]) makeZipTieHole();
        translate([holeOutset * -1,motorMountOffset + ((motorLength / 2) - motorMountHoleOffset),0]) makeZipTieHole();

        translate([holeOutset,motorMountOffset ,0]) makeZipTieHole();
        translate([holeOutset * -1,motorMountOffset,0]) makeZipTieHole();

        translate([holeOutset,motorMountOffset + (-1 * ((motorLength / 2)) + motorMountHoleOffset),0]) makeZipTieHole();
        translate([holeOutset * -1,motorMountOffset + (- 1 * ((motorLength / 2)) + motorMountHoleOffset),0]) makeZipTieHole();
}

module makeZipTieHole(){
    rotate ([0,0,90]) cylinder(botHeight,motorMountHoleDiameter / 2,motorMountHoleDiameter / 2);
}

module weaponPin() {
    translate ([0,(botDiameter * - 0.5) + weaponInset,(floorThickness - motorDepthBelowFloorSurface) + motorDiameter / 2])
    rotate ([90,0,0])
    cylinder(weaponThickNess + weaponPinExtraLength,(weaponMountHoleDiameter - weaponPinDiameterReduce) / 2, (weaponMountHoleDiameter - weaponPinDiameterReduce) / 2, center = true);
}

module weapon(){
    difference() {
        translate ([0,(botDiameter * - 0.5) + weaponInset,(floorThickness - motorDepthBelowFloorSurface) + motorDiameter / 2])
        rotate ([90,0,0])
        translate ([weaponWidth * -.5,(botHeight * -.5) - weaponBottomVerticalExtension,weaponThickNess * -.5])

        cube([weaponWidth,botHeight + weaponTopVerticalExtension + weaponBottomVerticalExtension, weaponThickNess], center = false);
        translate([0,0,weaponBottomVerticalExtension * -1]) {
            mainShell(botHeight + weaponBottomVerticalExtension);

            translate([0,weaponSlotExtraWidth * -1, 0]) mainShell(botHeight + weaponBottomVerticalExtension);
        }



        if (includeWeaponMountHole) weaponMountHole();
    }
}
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

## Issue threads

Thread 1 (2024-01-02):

Potential error in the schematic

tymcneer, 2024-01-02:
The Motor 1 tag has wire tag of 9 and a microcontroller pin designation of 4. I believe the microcontroller pin is supposed to be pin 9 for Motor 1 and pin 10 for Motor 2 ( I can't confirm pin 10 for Motor 2, as I built the single wheel test platform)

nothinglabs, 2024-01-02:
Yup - that was definitely wrong.  Good catch.

Just checked in a correction.  Thanks for letting me know!

Does your test platform work? I haven't heard back from anyone who has
tried building the new version - you might be the first!

-Rich

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

tymcneer, 2024-01-02:
Thanks for confirming! I was not entirely sure the problem wasn't on my end.

As to functionality, yes, it functions. There is an issue where I need to adjust the vector of translation, in relation to the heading light, but that seems to be a simple software fix. The current plan is to create a new test chassis, with mounts for the other components, and then try it at the March Maryland Area Combat Robotics Organization (MACRO) competition. I will have more information by April.

Ty

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

nothinglabs, 2024-01-03:
great to hear you got it working!

To adjust the heading LED offset - just tweak DEFAULT_LED_OFFSET_PERCENT in melty_config.h (or use the interactive setup).

If you've used the interactive setup - but want the settings in melty_config.h to over-ride - just change EEPROM_WRITTEN_SENTINEL_VALUE to a new value.

Side note - I just figured out that an 11.1v fully-charged LiPo battery (12.6v) is a bit too much for the Adafruit ItsyBitsy v-reg (probably same for Arduino Micro).  It usually works - but definitely can cause issues.  I just updated the docs to suggest a dedicate voltage regulator for over 7.4v.

Feel free to reach out directly with any questions to rich@nothinglabs.com.

Good luck with the competition!

-Rich

tymcneer, 2024-01-03:
Glad to know you had experimented with higher voltages, and warned others that there could be an issue with the regulator.

Once I get some time, hopefully this week, I am going to get the test bed working correctly and then move on to a revised chassis. Once that is complete, testing will resume on Monday.

Ty

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

Closed 2024-01-24.

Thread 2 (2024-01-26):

Custom Open Melt PCB Hardware Changes

TJMakes, 2024-01-26:
Hello!

Thank you so much for all the hard work that has gone into your firmware, testing and documentation. I read that your goal is "_Make translational drift accessible to more combat robot builders – and try to keep it that way into the future._" It certainly achieved this for me! This firmware is far beyond what I am capable of myself.

I am allergic to wiring and so I am designing a PCB to support Open Melt and hopefully make it easier for people to use (+have a unified hardware architecture to support). I am still finishing laying it out but am keen for your feedback on the schematic.

[SCH_OpenMelt2 Schematic_2024-01-26 (1).pdf](https://github.com/nothinglabs/openmelt2/files/14060800/SCH_OpenMelt2.Schematic_2024-01-26.1.pdf)

### Key Features:
- 6-32V Input voltage directly from Battery (2-6S)
- Buck Regulator with 5V 1A output
- 2 x 30A Brushed Motor Switches.
- Integrated H3LIS331 IMU
- Pro Micro Headers
- 5V Header LED Output (no current regulation onboard)

I have made the following design choices and I would like to hear if you have any feedback. This is your platform so I am very keen to design it around your priorities as well. I will hopefully be able to contribute via pull requests to firmware changes needed to support the PCB.

### Design Updates

**Swapped from Arduino Micro to Sparkfun Pro Micro, but kept as external plug in module**
The "Arduino micro" is not the most common atmega32u4 platform, and the "Pro Micro" originally released by sparkfun (but cloned to oblivion) is the ubiquitous board. Even searching Arduino micro results in more results for Pro Micro than it does the original Arduino board, which I feel is confusing to potential users that are interested in Open Melt. The Pro Micro is much cheaper and readily available for me in Australia. I chose not to integrate the Atmega32u4 directly, as then users will have to mess around with burning bootloaders onto the chip which is quite a hurdle if you do not have that experience.

**Integrated H3LIS331 & Level Shifting to OpenMelt PCB**
The H3LIS331 is quite an expensive niche chip, and I wasn't able to source the Adafruit board easily, so I needed to use the sparkfun board for initial testing with an external level shifter. This was a bit of a pain and I'm a bit suspicious of the long-term availability of these breakout boards. So I have integrated the chip and the level shifting circuitry onto the PCB itself, with a dedicated 3V3 LDO to drive it.

**Integrated Buck Regulator Module**
I build primarily featherweight robots, here 6S is the most common voltage at that level. So I have inserted an off the shelf 6-32V Input, 5V 1A output regulator module. I did this as a very lazy  and quick option. I would like to have a more powerful 3A module in future using an integrated version of the MP1584 modules that are available everywhere.

### Things I am not yet happy with
- The Power and Motor Connectors are uninsulated, and I would like to find better solutions. Ideally Insulated PCB mount connectors that are compatible with 3,4 or 6mm RC bannana conncetors.
- I will improve the buck regulator in the next version.
- I would like to move away from Mosfets to proper motor driver ICs, but it might make sense to keep the power stage off this control board entirely and require users to use standard ESCs (brushed or brushless).
- The current size (60x60mm) is not small enough for antweight. I can make another design that is 2/3S and 5A power level which can be much smaller. I have taken care to separate raw battery power traces from potential sources of short circuit on the PCB for safety but this is not the most compact.

### Future Design Goals
- I would like to design and 3D print a nice case.
- I would like to be able to switch between OpenMelt and Traditional Drive modes (simple passthrough of RC signals), but there is a lot that goes into this.
- I would like finished modules to be available for people on Tindie or similar. You can have any sales revenue if you like to support your development.

nothinglabs, 2024-01-29:
Thanks for putting this together!  I think this is a great idea.  I do have a bunch of thoughts - and will follow-up with them in the next couple days.

-Rich

nothinglabs, 2024-02-03:
Sorry for the delay (I was out of town on a bike tour for a bit).

This is all great!

I had thought about doing a PCB board to go with the project - but wanted to keep the project focused on the firmware / minimal test-build.  (I think success on a lot of projects is about keeping the scope down to something you can execute on)

I went with the Arduino Micro mostly for name-recognition (to help make it clear "this is easy - It's just Arduino!").  If all the needed pins are exposed - should be no problem using any other atmega32u4 board.  I think including the "Pro Micro" on the board directly makes a lot of sense (no reason to re-invent the wheel).  Preserving the USB programmer is great as it makes firmware modification easy.

The MOSFET to drive the LED is a nice addition.  Driving the LED from the AVR at ~20ma is "just bright enough."  Earlier builds of Open Melt based on the Pololu Baby-O boards could drive a 1-watt LED (blinding!) - which is much better for visibility in a brightly lit arena.

Having motor drivers on-board / keeping off-board is a good question.  One option may be to have motor drivers onboard - but also have the motor signal pins broken out on connectors.

One thing to think about is accelerometer placement.  At a radius of 5cm - you end-up around 400g at around 2800rpm.  Being able to keep the accelerometer close to the center of rotation is a consideration - and if the board is too big - might cause challenges (rotating the board off-axis can help).  This is an upside of a separate breakout board for the accelerometer (of course doing a custom breakout board would be an option).

https://www.sigmaaldrich.com/US/en/support/calculators-and-apps/g-force-calculator

I went with the H3LIS331 due to availability on breakout boards (wanted to assure the project was buildable without a custom PCB).  If it becomes an issue in the future - the H3LIS331 could probably be swapped with a different part fairly easily (from a firmware perspective).

A long-time ago I built a version of Open Melt that supported "normal" drive mode.  It worked with some bidirectional motor controllers from Pololu.  It's something I've left out of the code for simplicity.  Doing different behavior when the throttle is at 0% is pretty easy - but currently moving the stick to the front / back do some things in the current code (config-mode and RPM flash-out).  There probably some smart / easy ways to deal with this (10% to 40% throttle = normal drive).
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
nothinglabs, 2024-02-20:
Looking good!

Doing 1:1 passthrough on the RX's PWM signal should not be that hard.  I think the trick will be is finding a motor driver that will handle both RX-style PWM - and then be able to handle the refresh rates needed for transnational drift.  It may be that any RC's PWM signal (probably50hz) would need to get "upconverted" to 490hz.

If you get specific set of hardware you want to try with something with for the pasthrough - let me know.  Probably a few hours work to get something testable.

nevsie, 2024-04-08:
It may not be important, or relevant - but I am doing my own build currently and have thoughts...
1 - Power management.  On board is handy, however, my current board, being a USB C versions allows me to push in 3v-15v.  Reduces my need there.
2 - Motor Switching - I was hoping to use PWM out to some small brushed esc's. Maybe eventually move to brushless, hence the approach. A pad for this would be good. Although, comment above about rates has me worrying now!
3 - Heading LED through shotty is good, as people may want to run multiple LEDs, either for when it inverts, or flashy effects.
4 - Accel on board. I would not. It massively limits position and design. In my case I am doing a UK Ant (US Fairy), and I am hoping to use the H3lis200dl and have the gyro just off centre.
5 - Likewise radio off board, as people have preferences.

I think the board should do the core - but also "not make assumptions". Assumptions about power, motor, esc, take away peoples flair!

But to you both. Amazing work. I've a long way to go. But just some thoughts.

TJMakes, 2024-04-09:
Hi Nevsie,

Thanks for the input and definitely valuable! Also thank you for reminding me to get back to this. There are not many events in Aus so I get a bit distracted from my robotics projects in the off-season.

I will spin up a layout that has the motor drivers and power circuitry offboard (or at least as separate modules). I think this is the only way to accomodate all weight classes. You are right that I shouldn't have tried to make it do everything. If someone is running 12S in their robot they can regulate to 5V themselves haha.

My desire on integrating the accelerometer is that, with motor drivers removed, the entire openmelt pcb would be able to be not much bigger than the gyro breakout itself. I have a particular loathing for any extra wires in my smaller robots as they end up taking up a lot of the available space in the chassis.

I can do something where the the accelerometer can be snapped off and used remotely, and can be a lot smaller than the off-the-shelf modules, as it won't need all the pullup resistors, level shifting etc.

I will mock up a layout and send through, and we can discuss. There's 3 of us in the chain now and so I am happy to be outvoted!

TJMakes, 2024-04-09:
Unfortunately I can't see your pictures Nevsie. I compete in the Featherweight class so 13.6kg here.

See attached for mockup of a simplified PCB with just RC channels in, PWM out, with accelerometer onboard. The PCB is **31x18mm** and is a bit smaller than the pro micro into which it plugs in (which is smaller again than the arduino micro). Can't get smaller than this without integrating the MCU and moving away from standard RC connectors, which would be a headache.

I have centered the HIS331 exactly in the centre of the PCB (marked on the underside by the white dot. I would use this module by soldering futaba pigtails onto one end to plug into receiver, then with a 3x3p pin header on the other side to plug in ESC/s and LED.

Main constraint with this approach is that you need to make sure your BEC can drive the current of whatever header LED you use. I would imagine that it would be very rare that a robot does not have 100mA or similar excess current capacity on its 5V rail.

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

Here is 3D model of PCB if you would like to play around with how it could fit into your bot. Note that it would have the sparkfun pro micro on top of it as well.

[OpenMeltSimple.zip](https://github.com/nothinglabs/openmelt2/files/14925200/OpenMeltSimple.zip)

nevsie, 2024-04-10:
That is looking really nice.
I know what you mean about integrating radio (don't, I've been discussing how little fun this is with mark, malenki man!). I am currently using FS2A board, but also have also done ibus over UART. And tonight have been playing with bluepad32, connecting gaming controllers with Bluetooth. I might make a ESP32-pico-d4 board if I can bring myself to learning kicad, and so forth.

I forgot the images previously if my test ant chassis.
Note it's n20 motor 3000rpm, but next stop brushless... Maybe!
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

nothinglabs, 2024-04-17:
nice looking bot!

Imdad3456, 2024-11-11:
Is there a way I could get a gerber file of this pcb so I can make my own

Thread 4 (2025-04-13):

Adafruit_SleepyDog.h not detected

jk31454, 2025-04-13:
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

Program doesn't want to compile, even though the package is in the correct directory

Fix- replace <> with ""

nothinglabs, 2025-04-19:
The Adafruit's SleepyDog library is intended to be installed using Arduino's library manager - not copied into the source tree.

Hope this helps!
-Rich

jk31454, 2025-04-19:
ok, thanks. I did get it working anyway.

Closed 2025-04-19.

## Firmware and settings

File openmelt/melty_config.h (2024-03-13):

//This file is intended to include all commonly modified settings for Open Melt

#ifndef MELTY_CONFIG_GUARD  //header guard
#define MELTY_CONFIG_GUARD

//----------AVR SPECIFIC FUNCTIONALITY----------
//This code has not been tested on ARM / non-AVR Arduinos (but may work)
//Doesn't currently support persistent config storage for non-AVR Arduinos (see config_storage.cpp for details)
//490Hz PWM-throttle behavior is specific to Atmega32u4 (see below)

//----------DIAGNOSTICS----------
//#define JUST_DO_DIAGNOSTIC_LOOP                 //Disables the robot / just displays config / battery voltage / RC info via serial

//----------EEPROM----------
#define ENABLE_EEPROM_STORAGE                     //Comment out this to disable EEPROM (for ARM)
#define EEPROM_WRITTEN_SENTINEL_VALUE 42          //Changing this value will cause existing EEPROM values to be invalidated (revert to defaults)

//----------TRANSLATIONAL DRIFT SETTINGS----------
//"DEFAULT" values are overriden by interactive config / stored in EEPROM (interactive config will be easier if they are about correct)
//To force these values to take effect after interactive config - increment EEPROM_WRITTEN_SENTINEL_VALUE
#define DEFAULT_ACCEL_MOUNT_RADIUS_CM 3.9         //Radius of accelerometer from center of robot
#define DEFAULT_LED_OFFSET_PERCENT 7              //Adjust to make heading LED line up with direction robot travels 0-99 (increasing moves beacon clockwise)
                                                   
#define DEFAULT_ACCEL_ZERO_G_OFFSET 0.0f          //Value accelerometer returns with robot at rest (in G) - adjusts for any offset
                                                  //H3LIS331 claims +/-1g DC offset - typical - but +/-2.5 has been observed at +/-400g setting (enough to cause tracking error)
                                                  //Just enterring and exiting config mode will automatically set this value / save to EEPROM (based on current accel reading reflecting 0g)
                                                  //For small-radius bots - try changing to H3LIS331 to +/-200g range for improved accuracy (accel_handler.h)

#define LEFT_RIGHT_HEADING_CONTROL_DIVISOR 1.5f   //How quick steering is (larger values = slower)

#define MIN_TRANSLATION_RPM 400                   //full power spin in below this number (increasing can reduce spin-up time)


//----------PIN MAPPINGS----------
//RC pins must be Arduino interrupt pins
//we need 3 interrupt pins - which requires an Arduino with Atmega32u4 or better (Atmega328 only support 2 interrupts)
//Common RC receiver setup LEFTRIGHT = CH1, FORBACK = CH2, THROTTLE = CH3
//Note: Accelerometer is connected with default Arduino SDA / SCL pins

#define LEFTRIGHT_RC_CHANNEL_PIN 7                //To Left / Right on RC receiver
#define FORBACK_RC_CHANNEL_PIN 1                  //To Forward / Back on RC receiver (Pin 1 on Arduino Micro labelled as "TX" - https://docs.arduino.cc/hacking/hardware/PinMapping32u4)
#define THROTTLE_RC_CHANNEL_PIN 0                 //To Throttle on RC receiver (Pin 0 on Arduino Micro labelled as "RX" - https://docs.arduino.cc/hacking/hardware/PinMapping32u4)

#define HEADING_LED_PIN	8                         //To heading LED (pin 13 is on-board Arduino LED)

//no configuration changes are needed if only 1 motor is used!
#define MOTOR_PIN1 9                              //Pin for Motor 1 driver
#define MOTOR_PIN2 10                             //Pin for Motor 2 driver

#define BATTERY_ADC_PIN A0                        //Pin for battery monitor (if enabled)


//----------THROTTLE CONFIGURATION----------
//THROTTLE_TYPE / High-speed PWM motor driver support:
//Setting THROTTLE_TYPE to FIXED_PWM_THROTTLE or DYNAMIC_PWM_THROTTLE pulses 490Hz PWM signal on motor drive pins at specified duty cycle (0-255)
//Can be used for 2 possible purposes:
//  1. Used as control signal for a brushless ESC supporting high speed (490Hz) PWM (tested with Hobbypower 30A / "Simonk" firmware)
//          Assumes Arduino PWM output is 490Hz (such as Arduino Micro pins 9 and 10) - should be expected NOT to work with non-AVR Arduino's without changes
//  2. 490hz signal maybe fed into a MOSFET or other on / off motor driver to control drive strength (relatively low frequency)
//Thanks to Richard Wong for his research in implementing brushless ESC support

enum throttle_modes {
  BINARY_THROTTLE,      //Motors pins are fully on/off - throttle controlled by portion of each rotation motor is on (no PWM)

  FIXED_PWM_THROTTLE,   //Motors pins are PWM at PWM_MOTOR_ON, PWM_MOTOR_COAST or PWM_MOTOR_OFF
                        //throttle controlled by portion of each rotation motor is on

  DYNAMIC_PWM_THROTTLE  //Scales PWM throttling between PWM_MOTOR_COAST and PWM_MOTOR_ON
                        //Range of throttle scaled over is determined by DYNAMIC_PWM_THROTTLE_PERCENT_MAX
                        //PWM is locked at PWM_MOTOR_ON for throttle positions higher than DYNAMIC_PWM_THROTTLE_PERCENT_MAX
                        //Robot speed is additionally controlled by portion of each rotation motor is on (unless DYNAMIC_PWM_MOTOR_ON_PORTION is defined)
                        //This mode reduces current levels during spin up at part throttle
};

#define THROTTLE_TYPE BINARY_THROTTLE      //<---Throttle type set here!

#define DYNAMIC_PWM_MOTOR_ON_PORTION 0.5f       //if defined (and DYNAMIC_PWM_THROTTLE is set) portion of each rotation motor is on is fixed at this value
                                                //About 0.5f for best translation (higher for increased RPM)

#define DYNAMIC_PWM_THROTTLE_PERCENT_MAX 1.0f   //Range of RC throttle DYNAMIC_PWM_THROTTLE is applied to 
                                                //0.5f for 0-50% throttle (full PWM_MOTOR_ON used for >50% throttle)
                                                //1.0f for 0-100% throttle

//----------PWM MOTOR SETTINGS---------- 
//(only used if a PWM throttle mode is chosen)
//PWM values are 0-255 duty cycle
#define PWM_MOTOR_ON 230                          //Motor PWM ON duty cycle (Simonk: 140 seems barely on / 230 seems a good near-full-throttle value)
#define PWM_MOTOR_COAST 100                       //Motor PWM COAST duty cycle - set to same as PWM_ESC_MOTOR_OFF for fully unpowered (best translation?)
#define PWM_MOTOR_OFF 100                         //Motor PWM OFF duty cycle (Simonk: 100 worked well in testing - if this is too low - ESC may not init)


//----------BATTERY MONITOR----------
#define BATTERY_ALERT_ENABLED                     //if enabled - heading LED will flicker when battery voltage is low
#define VOLTAGE_DIVIDER 11                        //(~10:1 works well - 10kohm to GND, 100kohm to Bat+).  Resistors have tolerances!  Adjust as needed...
#define BATTERY_ADC_WARN_VOLTAGE_THRESHOLD 7.0f  //If voltage drops below this value - then alert is triggered
#define ARDUINIO_VOLTAGE 5.0f                     //Needed for ADC maths for battery monitor
#define LOW_BAT_REPEAT_READS_BEFORE_ALARM 20      //Requires this many ADC reads below threshold before alarming


//----------SAFETY----------
#define ENABLE_WATCHDOG                           //Uses Adafruit's sleepdog to enable watchdog / reset (tested on AVR - should work for ARM https://github.com/adafruit/Adafruit_SleepyDog)
#define WATCH_DOG_TIMEOUT_MS 2000                 //Timeout value for watchdog (not all values are supported - 2000ms verified with Arudino Micro)
#define VERIFY_RC_THROTTLE_ZERO_AT_BOOT           //Requires RC throttle be 0% at boot to allow spin-up for duration of MAX_MS_BETWEEN_RC_UPDATES (about 1 second)
                                                  //Intended as safety feature to prevent bot from spinning up at power-on if RC was inadvertently left on.
                                                  //Downside is if unexpected reboot occurs during a fight - driver will need to set throttle to zero before power 

#endif

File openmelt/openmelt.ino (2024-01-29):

//See melty_config.h for configuration parameters

#include "rc_handler.h"
#include "melty_config.h"
#include "motor_driver.h"
#include "accel_handler.h"
#include "spin_control.h"
#include "config_storage.h"
#include "led_driver.h"
#include "battery_monitor.h"

#ifdef ENABLE_WATCHDOG
#include <Adafruit_SleepyDog.h>
#endif

void service_watchdog() {
#ifdef ENABLE_WATCHDOG
    Watchdog.reset();
#endif
}

//loops until a good RC signal is detected and throttle is zero (assures safe start)
static void wait_for_rc_good_and_zero_throttle() {
    while (rc_signal_is_healthy() == false || rc_get_throttle_percent() > 0) {
      
      //"slow on/off" for LED while waiting for signal
      heading_led_on(0); delay(250);
      heading_led_off(); delay(250);
      
      //services watchdog and echo diagnostics while we are waiting for RC signal
      service_watchdog();
      echo_diagnostics();
  }
}
  

//Arduino initial setup function
void setup() {
  
  Serial.begin(115200);

  //get motor drivers setup (and off!) first thing
  init_motors();
  init_led();

#ifdef ENABLE_WATCHDOG
  //returns actual watchdog timeout MS
  int watchdog_ms = Watchdog.enable(WATCH_DOG_TIMEOUT_MS);
#endif

  init_rc();
  init_accel();   //accelerometer uses i2c - which can fail blocking (so only initializing it -after- the watchdog is running)
  
//load settings on boot
#ifdef ENABLE_EEPROM_STORAGE  
  load_melty_config_settings();
#endif

//if JUST_DO_DIAGNOSTIC_LOOP - then we just loop and display debug info via USB (good for testing)
#ifdef JUST_DO_DIAGNOSTIC_LOOP
  while (1) {
    service_watchdog();
    echo_diagnostics();
    delay(250);   //delay prevents serial from getting flooded (can cause issues programming)
  }
#endif

#ifdef VERIFY_RC_THROTTLE_ZERO_AT_BOOT 
  wait_for_rc_good_and_zero_throttle();     //Wait for good RC signal at zero throttle
  delay(MAX_MS_BETWEEN_RC_UPDATES + 1);     //Wait for first RC signal to have expired
  wait_for_rc_good_and_zero_throttle();     //Verify RC signal is still good / zero throttle
#endif

}

//dumps out diagnostics info
static void echo_diagnostics() {

  Serial.print("Raw Accel G: "); Serial.print(get_accel_force_g());
  Serial.print("  RC Health: "); Serial.print(rc_signal_is_healthy());
  Serial.print("  RC Throttle: "); Serial.print(rc_get_throttle_percent());
  Serial.print("  RC L/R: "); Serial.print(rc_get_leftright());
  Serial.print("  RC F/B: "); Serial.print(rc_get_forback());

#ifdef BATTERY_ALERT_ENABLED
  Serial.print("  Battery Voltage: "); Serial.print(get_battery_voltage());
#endif 
  
#ifdef ENABLE_EEPROM_STORAGE  
  Serial.print("  Accel Radius: "); Serial.print(load_accel_mount_radius());
  Serial.print("  Heading Offset: "); Serial.print(load_heading_led_offset());
  Serial.print("  Zero G Offset: "); Serial.print(load_accel_zero_g_offset());
#endif  
  Serial.println("");

}

//Used to flash out max recorded RPM 100's of RPMs
static void display_rpm_if_requested() {
  //triggered by user pushing throttle up while bot is at idle for 750ms
  if (rc_get_forback() == RC_FORBACK_FORWARD) {
    delay(750);
     //verify throttle at zero to prevent accidental entry into RPM flash
    if (rc_get_forback() == RC_FORBACK_FORWARD && rc_get_throttle_percent() == 0) {
       
      //throttle up cancels RPM count
      for (int x = 0; x < get_max_rpm() && rc_get_throttle_percent() == 0; x = x + 100) {
        service_watchdog();   //flashing out RPM can take a while - need to assure watchdog doesn't trigger
        delay(600); heading_led_on(0);
        delay(20); heading_led_off();
      }
      delay(1500);  //flash-out punctuated with delay to make clear RPM count has completed
    }
  }
}

//checks if user has requested to enter / exit config mode
static void check_config_mode() {
  //if user pulls control stick back for 750ms - enters (or exits) interactive configuration mode
  if (rc_get_forback() == RC_FORBACK_BACKWARD) {
    delay(750);
    if (rc_get_forback() == RC_FORBACK_BACKWARD) {
      toggle_config_mode(); 
      if (get_config_mode() == false) save_melty_config_settings();    //save melty settings on config mode exit
      
      //wait for user to release stick - so we don't re-toggle modes
      while (rc_get_forback() == RC_FORBACK_BACKWARD) {
        service_watchdog();
      }
    }
  }    
}

//handles the bot when not spinning (with RC good)
static void handle_bot_idle() {

    motors_off();               //assure motors are off
    
    //normal LED "fast flash" - indicates RC signal is good while sitting idle
    heading_led_on(0); delay(30);
    heading_led_off(); delay(120);

    //if in config mode blip LED again to show "double-flash" 
    if (get_config_mode() == true) {
      heading_led_off(); delay(400);
      heading_led_on(0); delay(30);
      heading_led_off(); delay(140);
    }

    check_config_mode();          //check if user requests we enter / exit config mode
    display_rpm_if_requested();   //flashed out RPM if user has requested

    echo_diagnostics();           //echo diagnostics if bot is idle
}

//main control loop
void loop() {

  service_watchdog();             //keep the watchdog happy

  //if the rc signal isn't good - assure motors off - and "slow flash" LED
  //this will interrupt a spun-up bot if the signal becomes bad
  while (rc_signal_is_healthy() == false) {
    motors_off();
    
    heading_led_on(0); delay(30);
    heading_led_off(); delay(600);
    
    //services watchdog and echo diagnostics while we are waiting for RC signal
    service_watchdog();
    echo_diagnostics();
  }

  //if RC is good - and throtte is above 0 - spin a single rotation
  if (rc_get_throttle_percent() > 0) {
    //this is where all the motor control happens!  (see spin_control.cpp)
    spin_one_rotation();  
  } else {    
    handle_bot_idle();
  }

}

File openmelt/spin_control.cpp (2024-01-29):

//this module handles calculation and timing loop for translational drift
//direction of rotation assumed to be CLOCKWISE (but should work counter-clockwise)

#include "arduino.h"
#include "melty_config.h"
#include "motor_driver.h"
#include "rc_handler.h"
#include "spin_control.h"
#include "accel_handler.h"
#include "config_storage.h"
#include "led_driver.h"
#include "battery_monitor.h"

#define ACCEL_MOUNT_RADIUS_MINIMUM_CM 0.2                 //Never allow interactive config to set below this value
#define LEFT_RIGHT_CONFIG_RADIUS_ADJUST_DIVISOR 50.0f     //How quick accel. radius is adjusted in config mode (larger values = slower)
#define LEFT_RIGHT_CONFIG_LED_ADJUST_DIVISOR 0.1f         //How quick LED heading is adjusted in config mode (larger values = slower)

#define MAX_TRANSLATION_ROTATION_INTERVAL_US (1.0f / MIN_TRANSLATION_RPM) * 60 * 1000 * 1000
#define MAX_TRACKING_ROTATION_INTERVAL_US MAX_TRANSLATION_ROTATION_INTERVAL_US * 2   //don't track heading if we are this slow (also puts upper limit on time spent in melty loop for safety)

static float accel_mount_radius_cm = DEFAULT_ACCEL_MOUNT_RADIUS_CM;
static float accel_zero_g_offset = DEFAULT_ACCEL_ZERO_G_OFFSET;
static float led_offset_percent = DEFAULT_LED_OFFSET_PERCENT;         //stored in EEPROM as an INT - but handled as a float for configuration purposes

static unsigned int highest_rpm = 0;
static bool config_mode = false;   //1 if we are in config mode

//loads settings from EEPROM
void load_melty_config_settings() {
#ifdef ENABLE_EEPROM_STORAGE 
  accel_mount_radius_cm = load_accel_mount_radius();
  accel_zero_g_offset = load_accel_zero_g_offset();
  led_offset_percent = load_heading_led_offset();
#endif  
}

//saves settings to EEPROM
void save_melty_config_settings() {
#ifdef ENABLE_EEPROM_STORAGE 
  save_settings_to_eeprom(led_offset_percent, accel_mount_radius_cm, accel_zero_g_offset);
#endif  
}

//updated the expected accelerometer reading for 0g 
//assumes robot is not spinning when config mode is entered
//value saved to EEPROM on config mode exit
static void update_accel_zero_g_offset(){
  int offset_samples = 200;
  for (int accel_sample_loop = 0; accel_sample_loop < offset_samples; accel_sample_loop ++) {
    accel_zero_g_offset += get_accel_force_g();
  }
  accel_zero_g_offset = accel_zero_g_offset / offset_samples;
}

void toggle_config_mode() {
  config_mode = !config_mode;

  //on entering config mode - update the zero g offset
  if (config_mode) update_accel_zero_g_offset();
  
  //enterring or exiting config mode also resets highest observed RPM
  highest_rpm = 0;
}

bool get_config_mode() {
  return config_mode;
}

int get_max_rpm() {
  return highest_rpm;
}

//calculates time for this rotation of robot
//robot is steered by increasing / decreasing rotation by factor relative to RC left / right position
//ie - reducing rotation time estimate below actual results in shift of heading opposite the direction of rotation
static float get_rotation_interval_ms(int steering_disabled) {
  
  float radius_adjustment_factor = 0;

  //don't adjust steering if disabled by config mode - or we are in RC deadzone
  if (steering_disabled == 0 && rc_get_is_lr_in_normal_deadzone() == false) {
    radius_adjustment_factor = (float)(rc_get_leftright() / (float)NOMINAL_PULSE_RANGE) / LEFT_RIGHT_HEADING_CONTROL_DIVISOR;
  }
  
  float effective_radius_in_cm = accel_mount_radius_cm;
  
  effective_radius_in_cm = effective_radius_in_cm + (effective_radius_in_cm * radius_adjustment_factor);

  float rpm;
  //use of absolute makes it so we don't need to worry about accel orientation
  //calculate RPM from g's - derived from "G = 0.00001118 * r * RPM^2"
  rpm = fabs(get_accel_force_g() - accel_zero_g_offset) * 89445.0f;
  rpm = rpm / effective_radius_in_cm;
  rpm = sqrt(rpm);

  if (rpm > highest_rpm || highest_rpm == 0) highest_rpm = rpm;

  float rotation_interval = (1.0f / rpm) * 60 * 1000;
  return rotation_interval;
}
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

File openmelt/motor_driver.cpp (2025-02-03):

//this module handles interfacing to the motors

#include "arduino.h"
#include "melty_config.h"
#include "motor_driver.h"

//motor_X_on functions are used for the powered phase of each rotation
//motor_X_coast functions are used for the unpowered phase of each rotation
//motor_X_off functions are used for when the robot is spun-down

void motor_on(float throttle_percent, int motor_pin) {

  if (THROTTLE_TYPE == BINARY_THROTTLE) {
    digitalWrite(motor_pin, HIGH);
  }

  if (THROTTLE_TYPE == FIXED_PWM_THROTTLE) {
    analogWrite(motor_pin, PWM_MOTOR_ON);
  }

//If DYNAMIC_PWM_THROTTLE - PWM is scaled between PWM_MOTOR_COAST and PWM_MOTOR_ON
//Applies over range defined by DYNAMIC_PWM_THROTTLE_PERCENT_MAX - maxed at PWM_MOTOR_ON above this
  if (THROTTLE_TYPE == DYNAMIC_PWM_THROTTLE) {
    float throttle_pwm = PWM_MOTOR_COAST + ((throttle_percent / DYNAMIC_PWM_THROTTLE_PERCENT_MAX) * (PWM_MOTOR_ON - PWM_MOTOR_COAST));
    if (throttle_pwm > PWM_MOTOR_ON) throttle_pwm = PWM_MOTOR_ON;
    analogWrite(motor_pin, throttle_pwm);
  }
}

void motor_1_on(float throttle_percent) {
  motor_on(throttle_percent, MOTOR_PIN1);
}

void motor_2_on(float throttle_percent) {
  motor_on(throttle_percent, MOTOR_PIN2);
}

void motor_coast(int motor_pin) {
  if (THROTTLE_TYPE == FIXED_PWM_THROTTLE || THROTTLE_TYPE == DYNAMIC_PWM_THROTTLE) {
    analogWrite(motor_pin, PWM_MOTOR_COAST);
  }
  if (THROTTLE_TYPE == BINARY_THROTTLE) {
    digitalWrite(motor_pin, LOW);  //same as "off" for brushed motors
  }
}

void motor_1_coast() {
  motor_coast(MOTOR_PIN1);
}

void motor_2_coast() {
  motor_coast(MOTOR_PIN2);
}

void motor_off(int motor_pin) {
  if (THROTTLE_TYPE == FIXED_PWM_THROTTLE || THROTTLE_TYPE == DYNAMIC_PWM_THROTTLE) {
    analogWrite(motor_pin, PWM_MOTOR_OFF);
  }
  if (THROTTLE_TYPE == BINARY_THROTTLE) {
    digitalWrite(motor_pin, LOW);  //same as "off" for brushed motors
  }
}

void motor_1_off() {
  motor_off(MOTOR_PIN1);
}

void motor_2_off() {
  motor_off(MOTOR_PIN2);
}

void motors_off() {
  motor_1_off();
  motor_2_off();
}

void init_motors() {
  pinMode(MOTOR_PIN1, OUTPUT);
  pinMode(MOTOR_PIN2, OUTPUT);
  motors_off();
}

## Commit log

2023-04-27 adding brushless ESC support
2023-05-04 motor driver tweaks
2023-11-25 new throttle modes suppport
2023-12-01 adding reference design / directory path changes
    [lid.stl, shell.stl, spinbot_ant.scad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]
2023-12-04 mitigated problem with going into RPM count while reducing throttle
    [openmelt_schematic.kicad_pcb, openmelt_schematic.kicad_sch]
2023-12-07 docs, rc update
    [spinbot_ant.scad, weapon.stl]
2023-12-07 fixing issue with accepting usb programming
    [melty_config.h, openmelt.ino]
2023-12-08 doc updates, improvements to config mode, tracking error due to i2c reads now balanced
    [melty_config.h, motor_driver.cpp, openmelt.ino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]
2024-01-02 fixing error in schematic
    MOTOR_1 and MOTOR_2 were incorrect!
    [openmelt_schematic.kicad_sch]
2024-01-25 fixed possible bug in RC mutex lock
    [openmelt.ino, rc_handler.h, spin_control.cpp]
2024-03-13 Update melty_config.h
    reducing LEFT_RIGHT_HEADING_CONTROL_DIVISOR
    changing PWM defaults to values more likely to actually work with brushless PWMs
    [melty_config.h]
2025-02-01 Update motor_driver.cpp to include motor_driver.h
    motor_driver.cpp should include "motor_driver.h", not "led_driver.h".
